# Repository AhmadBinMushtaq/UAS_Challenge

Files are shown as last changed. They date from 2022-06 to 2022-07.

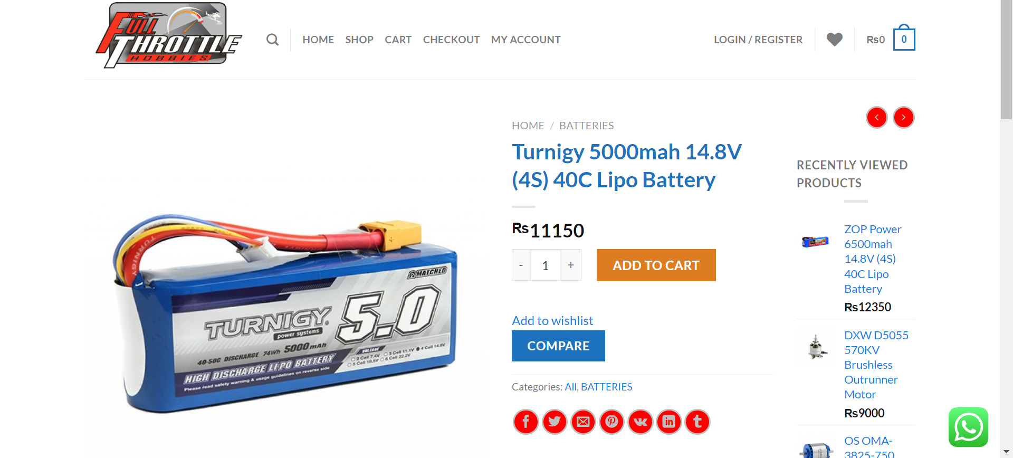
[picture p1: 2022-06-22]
Power & Propulsion System/Turnigy 5000mah 4S.png

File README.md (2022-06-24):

# ***UAS_Challenge***
## **The Hive**

The Hive is a team participating in UAS Challenge 2022 from NUST & FAST. Team consists of four mechanical engineering students, three electrical engineering students, a computer science student, a student from Geo-Informatics and a Business student.

## **Critical Design Report**

This repository keeps track of work distribution from Premilinary Design to Critical Design for all 4 teams:

- *Aerodynamic & CAD Design Team*
    - Sarah Naeem
    - Hamza Hussain
    - Jawad Akbar
    - Muhammad Hassan Kazmi

- *Power & Propulsion System Team*
    - Muhammad Hassaan Ghazali
    - Muhammad Ali Khalid

- *Control & Computing System Team*
    - Muhammad Adeel
    - Ahmad bin Mushtaq

- *Spraying Mechanism*
    - Saad bin Tariq

- *Social Media Outreach*
    - Muaz

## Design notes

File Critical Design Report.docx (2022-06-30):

Unmanned Aerial System (UAS) Challenge Pakistan 2022

National University of Sciences and Technology

Critical Design Report – The Hive

Name | University | Major | Standing
Sarah Naeem – Team Lead | NUST H-12 | Mechanical Eng. | Sophomore
Jawad Akbar | NUST H-12 | Mechanical Eng. | Sophomore
Hamza Hussain | NUST H-12 | Mechanical Eng. | Sophomore
Syed Muhmmad Hassan Kazmi | NUST H-12 | Mechanical Eng. | Sophomore
Ahmed Bin Mushtaq | NUST H-12 | Electrical Eng. | Sophomore
Muhammad Hassaan Ghazali | NUST H-12 | Electrical Eng. | Sophomore
Ali Khalid | NUST H-12 | Electrical Eng. | Sophomore
Muhammad Saad Bin Tariq | NUST H-12 | Geo Informatics Eng. | Sophomore
Muhmmad Adeel | FAST NUCES -Isl | Computer Sci. | Sophomore
Syed Muaz Ashrafi | NUST -H12 | BS. Economics | Junior

Team Members

Signature of Compiler – Sarah Naeem

Team Lead – The Hive

Approved by Dr. Kashif Javed

Assistant Professor at SMME NUST

Faculty Supervisor – The Hive

# List of Figures

# List of Tables

# 1. Summary of CDR Report

## 1.1. Proposed Design

This novel design includes a quad tiltrotor fixed-wing UAV configuration with each rotor attached at the ends of the four wings. With a wingspan of 1.44m and a fuselage length of 1.55m, the UAV has a mass of 4 kg, with a capacity of 3kg for pesticide carriage. The maximum spraying capacity of the drone is 3.5L/min.

With a full payload, it can cruise at 15ms⁻¹ consuming only 84 Watts for propulsion. The drone can fly at 30ms⁻¹ (max. airspeed for the required mission) with rotors burning only 452 Watts. The UAV can achieve a 55ms⁻¹ airspeed (not employed in the current mission) with its 12.5kg maximum thrust.

The spraying mechanism includes two types of nozzles for spraying and misting to maximize spray quality and reduce pesticide consumption per acre. The pump has a BLDC motor for controllable flow and a maximum pressure of 1MPa at 40 Watts power consumption.

Selig S1210 & S1223 are used as front & rear wings airfoils giving the optimum lift-to-weight ratio of wings.

This report provides a thorough analysis and calculation of the drone's mission performance, manufacturability, procurement, and mitigation of all possible safety hazards. This UAV is capable of:

- Stable flight in vertical mode due to widely spaced rotors from the fuselage
- Powerful horizontal flight via thrust from all four rotors positioned horizontally
- Stable transition in flight modes due to variable tilting angles of rotors

Compared to typical fixed-wing and multi-rotor configurations, this configuration produces optimum results as an agriculture UAV for the required mission profile. Comparison with other configurations results in:

- 5.5 to 6 times more power efficient in horizontal cruise than multi-copters. i.e., suitable for spray zones far away from Ground Control Station (suitable for the longest route of 4km in mission)
- Higher precision in spraying than fixed-wing configuration due to capability of hovering, gliding, and staying at transition state while spraying
- More stable hovering and spraying than its parent configuration quad plane

Team Name | | The Hive
Review Items | | Refer below to section 1.2.

Changes since PDR
Change | Reason
The High wing configuration is replaced with a mid-wing configuration.
Aft conventional tail type is replaced with cruciform aft tail configuration.
TMotors MN5008 are replaced with EMAX GT-2826 KV860 | Tmotors are not available locally, and the team changed it to EMAX due to temporary import restrictions
6S Battery is replaced with 4S | EMAX GT-2826 KV860 requires a 4S Battery
Supervisor | | Dr. Kashif Javed – Assistant Professor at SMME
Team Lead | | Sarah Naeem

Table 1. Summary chart for CDR

## 1.2. Payload & Mission summary

The UAV will carry the load at its maximum capacity, i.e., 3kg. It will follow the longest route of 4km towards the spraying zone at a cruise speed of 15ms⁻¹, ideally consuming 266 seconds and 7.75Wh energy. The UAV will cover the complete spray zone in 118-125 seconds, following its optimal path for the least time consumption, consuming 32Wh energy. UAV will then cruise back to landing at 10.7ms⁻¹, consuming 47 seconds and 0.65Wh energy. Hence, including 3 seconds of takeoff & 5 seconds of landing, and a transition time of 1.7 seconds, UAV will complete the mission in 441-455 seconds using the optimum energy consumption approach. It is adopted in this mission since time is not an issue and completing the mission before 10 minutes does not end up in bonus points. However, in real-world scenarios in an emergency, this UAV can complete the same mission in <290 seconds with only 28% more power consumption. Details are provided in the Engineering Analysis part.

2. Project Management

## 2.1. Progress Review

Sr # | Designation/subgroup | Name(s) | Assigned tasks and roles
3. | Mechanical design | - Hamza Hussain - Jawad Akbar - Sarah Naeem - Syed Muhammad Hassan Kazmi | - Aerodynamic Analysis - Structural and stress analysis - CAD model - Airframe manufacturing and material selection
4. | Electrical Circuitry | - Ali Khalid - Muhammad Hassaan Ghazali | - Propulsion system design - Electrical component selection - Battery performance analysis
5. | Spraying Mechanism | - Muhammad Saad bin Tariq | - Spraying mechanism selection - Selecting suitable pump, nozzles and supporting components - Spray tank design and manufacturing
6. | Business Model | - Syed Muaz Ashrafi | - Outreach - Industry support and collaboration - Business model
7. | Control & Computing System | - Ahmed bin Mushtaq - Muhammad Adeel | - Control and computing system design - Selecting supporting hardware

As the preliminary design review mentioned, the team is subdivided into groups for more accessible communication and effective workload distribution. The previous division has been revised since and is given in table 1.2

Table 2.1.1. Team Division and description

The workflow in Figure 2.1.2. shows task division from the PDR up to manufacturing and is divided according to the groups mentioned in Table 2.1.1.

A team tracker on the Google Drive Shared folder tracks the progress & timeline of each team till the CDR. Figure. b.b.b shows a part of The Hive Tracker.

All files in the project, including CAD models, reports, simulations, and source codes, are managed on Google Drive & GitHub repository [1] shown in Figures 2.1.3 & 2.1.4, respectively.

Moreover, the team conducted weekly joint team meetings, occasional team meetings with the faculty advisor and regular meetings of different groups to ensure timely completion of work and maintenance of the Project Progress tracker. Communication is done via MS Teams for meetings, WhatsApp groups for regular updates and Emails for notifications & announcements.

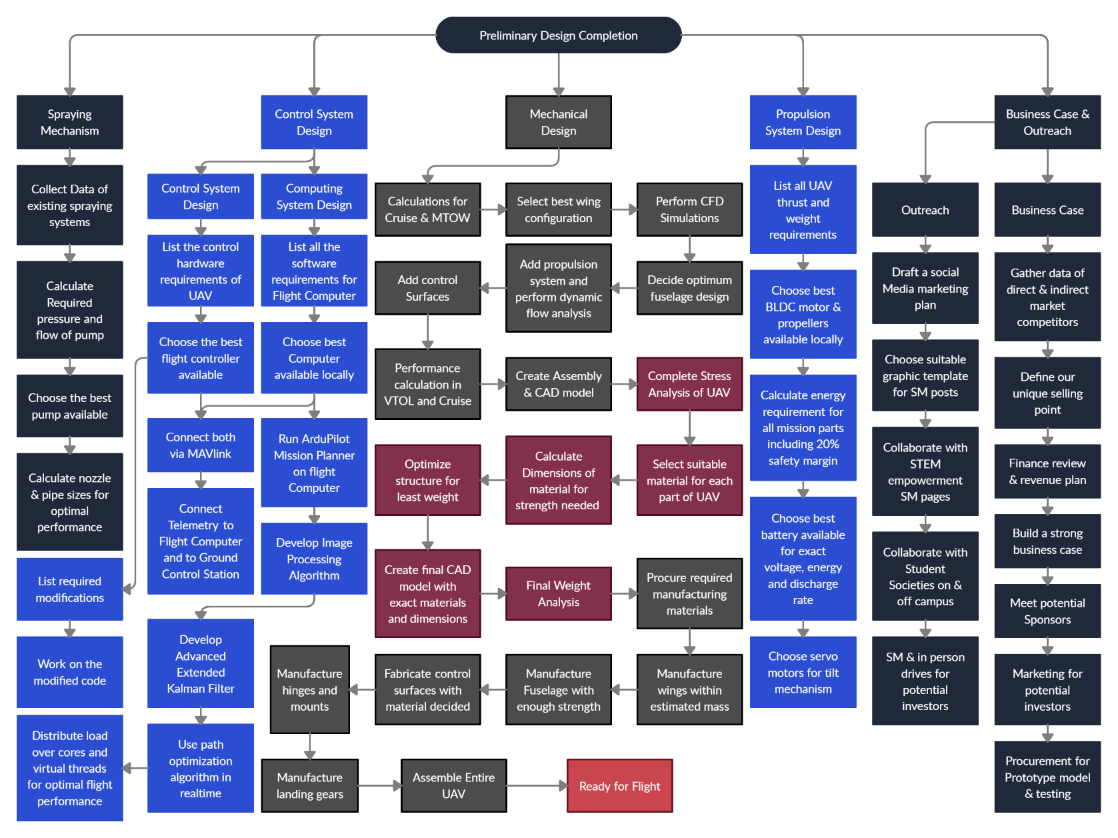
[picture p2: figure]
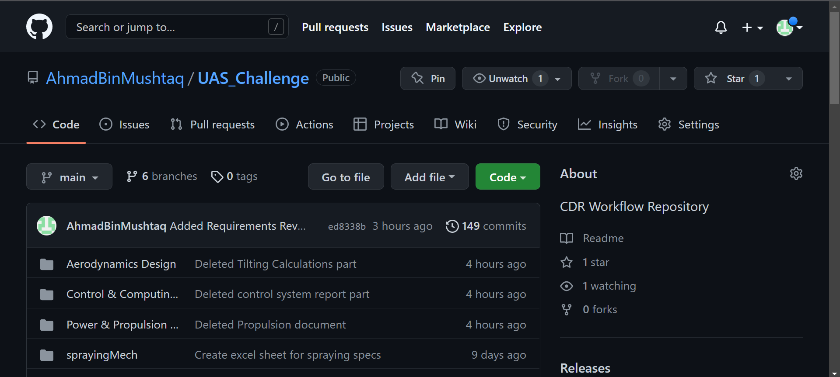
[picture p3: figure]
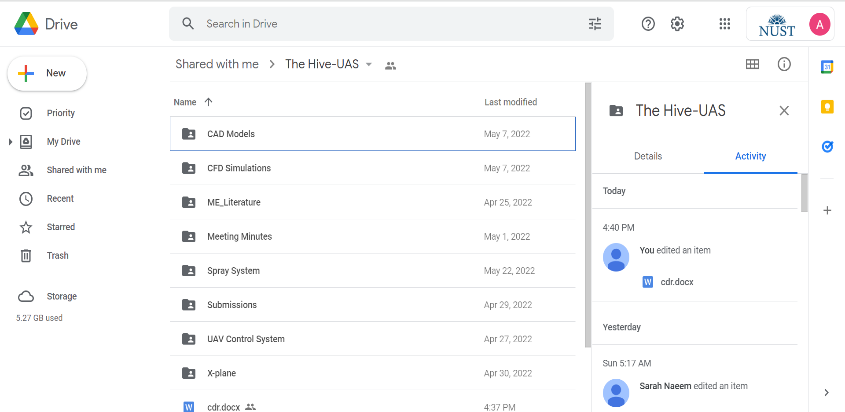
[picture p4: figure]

Figure 2.1.2. Project Workflow after PDR

Figure 2.1.4. Shared Google Drive Folder. [2]

Figure 2.1.3. Shared Google Drive Folder. [2]

## 2.2. Summary of Project Resources, Manufacturing and Risks

Project Part | Human Resource | Other Resources | Procurement | Manufacturing/ Development | Risks | Mitigation
Spraying Mechanism | Saad bin Tariq | None | Nozzles, Pump, Pipes and connectors | Optimized spray tank | Leakage, nozzle blockage, unavailable fluid to inflow. | Sump tank, nozzle filters and good connectors.
Flight Control System | Ahmad bin Mushtaq | ArduPilot source code, Pixhawk 2.4.8 | Open-source software + local available hardware | Fork the ardupilot repo and develop & compile firmware locally | Malfunctioning custom firmware | Continuous trial & error on in real-time flight
Computing System | Muhammad Adeel | Dronekit-python source code, Pytorch, Numpy | Open source | Fork the repo, develop according to needs and use them
Aerodynamic Design | Jawad Akbar | ANSYS Fluent 2022 | NA | Design revaluation in case of unstable flight | Unfavorable lift/drag generated during flight. | Thorough CFD simulation and performance calculations.
Structure Design & Stress Analysis | Hamza Hussain Sarah Naeem | ANSYS Workbench | NA | Design revaluation in case of abnormal stress generation | Airframe damage. | Thorough calculations and appropriate manufacturing techniques
CAD model | Hamza Hussain Muhammad Hassan Kazmi Sarah Naeem | Solidworks 2022 | NA | NA | Improper dimensions used in model leading to errors in manufacturing | Thorough revaluation
Manufacturing | | CAD model, equipment | Raw material | Airframe, tank, supports | Material damage and injuries | Manufacturing under experienced personnel guidance.
Propulsion System Design | Muhammad Hassaan Ghazali | None | All hardware components | None | Faulty parts. Part damage & malfunction mid flight | Procurement from well known vendors. Proper connections.
Battery & Power distribution design | Ali Khalid | None | All components | None | Battery hazards | Employ safe battery practices.
Social Media Outreach & Busin ess Case | Muaz | Social media accounts. Graphic design software | None | None | Digital backlash. | Practice healthy cyber habits.

Table 2. Project resources, manufacturing, and risks

# 3. Requirement Review

## 3.1. Mission Requirements and Verification

For table 4, the term ‘shall’ label a mandatory requirement and the term ‘should’ designates a highly desirable requirement.

Requirements | Verification
A detailed CAD assembly with emphasis on feasibility of design and manufacturing, control capacity and airworthiness. | Detailed CAD assembly created on Solidworks 2022 includes all components and structures employed in the final design.
UAS shall have either a fixed wing, rotary wing, or VTOL airframe configuration. | The design is tilt-rotor transition, fixed-wing VTOL aircraft
MTOM including payload and UAS shall not exceed 6.9 kg. | In weight analysis, the total mass with full payload is 6.9kg
UAS design should cater to rapid assembly/disassembly. | Easy to assemble airframe.
The UAS shall navigate waypoints and spray at targeted area in a fully autonomous manner and it should carry out fully autonomous take-off and landing. | Control & Computing System enable complete autonomy during take-off, spray & landing along with some advanced computing features.
The payload shall be a minimum of 500 ml. | There is 3L payload
The spray tank material should comply with UL 94, V0 flammability standards. It can be detachable or fixed to the UAV. For detachable tanks, re-attachment must be possible within the shortest amount of time. | Fixed spray tank manufactured from Carbon fiber is employed.
UAS airframe shall be designed from scratch. | Entire airframe is self-manufactured.
Cost for COTS components shall not exceed PKR 250,000. Proposed design solutions should be cost-efficient. | Total cost for COTS items adds up to 146K which is well below the specified limit.
Radio Equipment shall comply with PTA directives and licensed for use in Pakistan with a reliable operating range of 1km. Control of the UA and the FTS is ‘spread spectrum’ complaint to 100mW spread spectrum configuration to IR2030 and CE marked 4. | 433 MHz 500MW Telemetry used with range of 2.5km and spectrum available for personal/household devices
UA shall automatically return to landing zone/take-off or activate flight termination after a loss of data link of more than 30 seconds. | Advanced RTL feature in case of disconnected telemetry
UA shall automatically terminate flight in case of loss of GPS signal, for more than 3 minutes. | Flight termination feature included in the flight control system
‘Return Home’ signal shall be capable of activation by safety pilot. | Available in Mission Planner for Ground Control Station
A separate GPS data logger shall be fitted on top of the UAV, with clear exposure to the sky allowing real-time GPS information recording from take-off till landing. It shall also provide post-flight evaluation of the 3D trajectory. Placement of tracker should comply with vehicle safety and provide a glitch free flight safety review. | Provision has been left in design for GPS data logger and the control system is also compatible with it.
UAS design should plan on a target mission flight path with a distance of 2-4 km, from take-off to landing. | (With ref to battery consumption)
UAV to operate further than 500 m up to 1000 m where it may be flown safely and tracked within segregated airspace. | Telemetry used in UAV allows safe communication up to 2.5km range
UAV shall fly at a maximum altitude of 100m. | UAV is designed to cruise at about 30m AGL
UAV shall operate from within 10m x 30 m box, oriented at 30 degrees of wind direction. Landing must be within box, may be touchdown or roll out. | UAV shall use advanced computer vision to detect exact landing position and shall land with centimeters precision
Ground control station shall display all required information and be visible to operators, flight safety officers and judges. | Using telemetry, flight data logs are sent to ground control station using MAVlink and are displayed in mission planner
Should operate in winds of 20 kts gusting up to 25 kts and light rain. Shall be capable of landing and take-off in crosswind components to runway of 5 kts with gusts of 8 kts. | Drone shape designed for minimum air friction caused by wind High Thrust motors used for powerful propulsion against any windspeed below 55kts
Maximum airspeed in level flight shall not exceed 60 KIAS. | 35-40 KIAS adequate for completing the mission. Motor thrust will be adjusted accordingly.
Design and construction shall employ good design practice and use appropriate materials and components. | All materials and manufacturing methods are finalized after a thorough market analysis.
Design shall be supported by satisfactory structural integrity, stability and control, flight and navigation performance and reliability of critical systems. | Balsa airframe with carbon fiber reinforcements for structural integrity. Pixhawk, GPS and image processing for flight control and navigation.
Batteries used shall contain bright colors for easy detection in the event of a crash. | Battery pack will be bright colored.
At least 25% of upper, lower and each side shall be a bright color to facilitate visibility in air and event of a crash. | The entire external surface will employ surfacing of bright colored sheets.
UA shall remain within VLOS of remote pilot and remain below 100m AGL. | UAV path trajectory will make sure that it remains in boundaries
UA shall not be flown within 30 m of any person/structure not under the control of the Remote Pilot. During take-off and landing, it shall not be flown within a 10m distance. | UAV will not cruise below 30m in horizontal flight and would follow the exact trajectory where no humans intervene
UA shall remain in controlled flight and within the demonstration zone boundary during the entire flight | Safety precautions and settings are all set in flight control system
UA appearing uncontrolled or moving into ‘No Fly’ zone shall be subjected to manual override, failure to do so shall activate flight termination. | Safety precautions and settings are all set in flight control system
Consideration should be given to environmental impact. | BLDC motors with minimum noise production are used and environmentally friendly practices are employed for manufacturing.

Table 3. Requirement Review

## 3.2. Mission Success Criteria

The mission will be considered a success if the following criteria are met:

I. The UA covers the longest distance path to reach the SZ and navigate all WPs.
II. The UA completes the entire mission within 10 minutes.
III. The UA carries adequate payload to effectively spray entire spray zone.
IV. The UA performs successful flight termination and manual override.
V. The UA performs controlled flight without any damage to itself, property, or people.
VI. No safety violation occurs.

# 4. Design Description

## 4.1. Design Rationale

### 4.1.1. Airframe

A fixed-wing airframe design has opted for our UAV with a double pair of wings placed along the same axis. The wings are positioned midplane to the fuselage with a tilting rotor on each wing. This orientation provides the desired weight, strength, and performance efficiency in our mission objectives.

#### 4.1.1.1. Wings

Our design includes two rectangular mid-wing pairs, placed one after the other, with a taper ratio of 1 and a dihedral angle of zero. The design follows a primary unswept wing with an aspect ratio of 7.2 (low aspect ratio). A lower aspect ratio allows for easier maneuverability which is one of the core requirements of our mission.[3]

The wingspan of both wings is approximately 1440 mm. The airfoil in the leading pair of wings is S1210[4], oriented at zero degrees. The trailing wings use S1223[5], oriented at five degrees. Each wing section has a chord length of 200 mm. The chosen orientation and dimensions provide us with the ideal amount of lift, cruising speed, and altitudes required for the fly-off mission. A skeletal structure composed of balsa cross-sections and longitudinal spars will provide the main frame of the wings. This frame is reinforced by high-strength and lightweight circular rods running along the entire wingspan. The frame is surfaced to provide a smooth, streamlined surface for good aerodynamic performance.

Each wing will house a 9 g servo and a 20 g servo for the ailerons and tilting rotors. Rubber pipes will also run along its length with the spray nozzle attached at one end and to the pump at the other. Balsa wood cross-sections are placed perpendicular to the longitudinal-lateral plane. These cross-sections will be manufactured to match the airfoil used. Provisions for support rods, servo motors, wiring, and spray system are provided in these cross-sections.

The wings can be detached from the main assembly through simple reinforced connections to allow rapid assembly/disassembly. The details for these connections are discussed extensively in the manufacturing portion.

#### 4.1.1.2. Empennage

The Empennage refers to the tail section composed of a vertical and horizontal stabilizer. The UAV will ideally cruise at a zero-degree pitching angle at all times. The Sum of moments along all three axes must then always be zero. Due to the presence of 4 tilting rotors with relatively large propeller blades, a wake region will be generated. This wake must not blanket our tail sections, significantly reducing control efficiency. Our Empennage must also be lightweight and provide sufficient Control. For this, a cruciform tail orientation has been opted for. It is a type of aft tail configuration, intermediate between the conventional and T-tail, where the vertical and horizontal tails form a '+'. It combines the benefits of both and reduces several drawbacks of both tail configurations. [8] If aligned properly, a deep stall is avoided while maintaining low wing weight. Section 4.2. further shows calculations for the tailplane area. Control Surfaces are discussed ahead.

#### 4.1.1.3. Fuselage

For finalizing the fuselage design, a fuselage design requirements verification rubric was employed. Table 2. summarizes the final optimized design.[6]

Design Requirement | Verification
Adequate space to house payload and system hardware. | The mounting plate runs through the entire length of the fuselage with a payload tank mounted between it. Sufficient free space remains after the assembly of all components.
Low weight. | A monocoque structure is employed using balsa wood bulkheads and reinforced longitudinal spars. It is covered using heat shrink iron-on model aircraft covering (7.7g/ sq. ft.).
It provides a sturdy mounting platform for landing gear. | The landing gear mounts are reinforced at the main mounting plate.
Generates the lowest drag possible. | Low wetted and side area with a streamlined nose and symmetric, streamlined contours result in minimum drag.
It maintains external symmetry. | It has an elliptic shape, symmetric about the longitudinal axis
Airworthiness and compatibility for flight during weather conditions are mentioned in mission requirements. | A sturdy airframe and high-strength iron-on covering are resistant to high winds & gusts and light rain (tensile strength 1,757 kg/sq cm [7]).
Manufacturing feasibility | Semi-monocoque structures have better manufacturability than monocoque designs with increased strength than truss assemblies. Locally available material and manufacturing methods are employed for easy access and guidance on equipment handling.
Structural Integrity and strength | Truss elements are employed where necessary, reinforced by balsa cross-sections along the longitudinal axis and interlinked support structures allowing loads to be distributed over the entire assembly.

Table 4. Fuselage Design requirements and verification

#### 4.1.1.4. Landing Gear

The landing gear is essential for safe takeoff and landing and, if designed well, can act as a shock absorber during crash landings. It must be made of appropriate material to avoid shock caused by harsh and crash landing from traveling through the Airframe. For our design, skids are selected as landing gears. These are fixed supports that are attached to the UAVs. These are widely used in VTOLs as there is no need for wheels. The design employs a four-piece landing gear in table-leg orientation. In this type, four rods are connected to the fuselage via hinges. The rods are fastened to one another via a rubber or elastic strip, resembling a table leg. The material chosen is carbon due to its lightweight and high-strength properties. In the event of a crash landing, the rubber material and the hinges provide a damping mechanism; hence, the material breaking chances are low. The landing gear will widen when the UAV lands, but the rubber provides a restoring force to limit this expansion. This action-reaction force pair causes damping and absorbs the shock that the UAV experiences. In case of a crash landing, only the components damaged are repaired or replaced. Unlike most landing gear systems, the entire assembly will not be replaced.

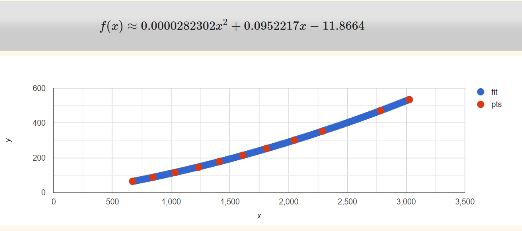
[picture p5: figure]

### 4.1.2. Propulsions

Power & Propulsion system of this UAV consists of following:

- 4 EMAX GT-2826 KV860 Brushless Motors
- 14*7’’ Carbon Fiber propellers
- Turnigy 5000mAh 4S Li-Po Battery with 40C Discharge Rate

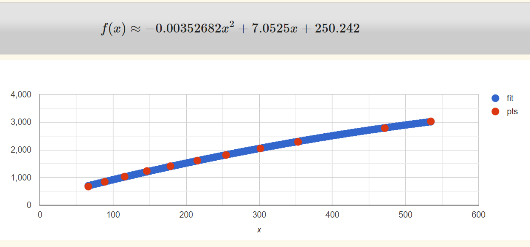
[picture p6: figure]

- 20g servos for tilting individual rotors

Figure 1. Power as a function of Thrust

Figure 2. Thrust as a function of Power

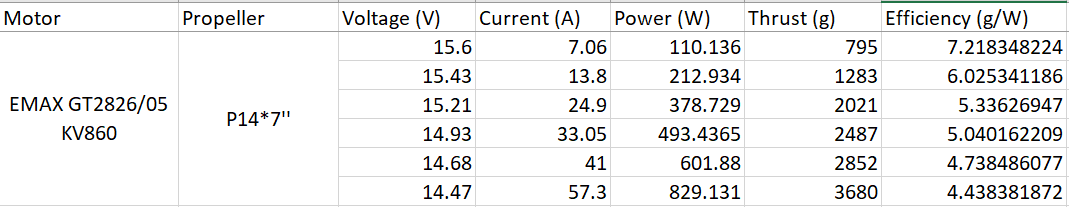
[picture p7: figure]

These components are selected after extensive calculations for optimum performance in fly-off mission. Note: MN5008 mentioned in PDR is replaced by EMAX because it wasn’t locally available.

Figure 3. EMAX GT2826/05 KV860 performance values

Data of all locally available motors is collected into the GitHub repository. The detailed datasheet of EMAX motors is not available online. All the data from the official website and thrust tests in workshops is gathered using finite values for this motor and datasheets available for similar motors; the closest continuous function was plotted against experimental values of thrust & power as shown in Fig. 4 & 5. Below are some power & thrust specifications of the motor used. Thrust for a single motor is written as a function of power using an online function calculator as:

thrust= -0.001632532∙power^2 +5.3238∙power+250 --- (i)

This continuous function gives a precise value for power between 50-850 Watts. Lift & Drag values for the Airframe on different airspeeds were obtained from simulations (detail in aerodynamics section). Again, using finite values, the estimated function was plotted for both lift & drag against airspeed.

lift=0.350317∙v^2 -0.202576 ∙v ---(ii)

drag=0.0350823∙v^2 +0.00372739∙v ---(iii) ∴v=airspeed

Cruise speed is calculated as: lift=0.350317∙v^2 -0.202576 ∙v= total mass of drone

Using this relation, the ideal cruise speed with a full payload, i.e., 6.9kg (flight towards Spray Zone), comes out to be 14.2ms⁻¹, and cruise speed without payload, i.e., 3.9kg (flight back to landing), comes out to be 10.7ms⁻¹.

Power consumption is calculated as:

drag= 0.0350823∙v^2 +0.00372739∙v=thrust of propulsion system

The thrust required for a total payload comes out to be 0.727237 kgf (0.181809 kgf for each motor). Power consumed to require this thrust is calculated by eq. (i) It comes out to be 84.5723W (21.143W per motor). Similarly, the thrust required without payload is 0.421658 kgf, and power consumption is 47.8332W. Calculating energy consumption & time taken for ideal cruise flight of 4km from take-off to spray zone and 500m from spray zone to landing:

time= (4000m)/(14.2ms^(-1))+ (500m)/(10.7ms^(-1))=328.42s (Approx. 5_2^1 minutes)

energy=84.5723W∙281.7s+47.8332W∙46.7s≈7.2383 Wh (<10% of available battery)

Ideal time & energy consumption calculations for takeoff, transition, spray zone & landing were done. Calculations are too complicated to be added in CDR. Results are given below.

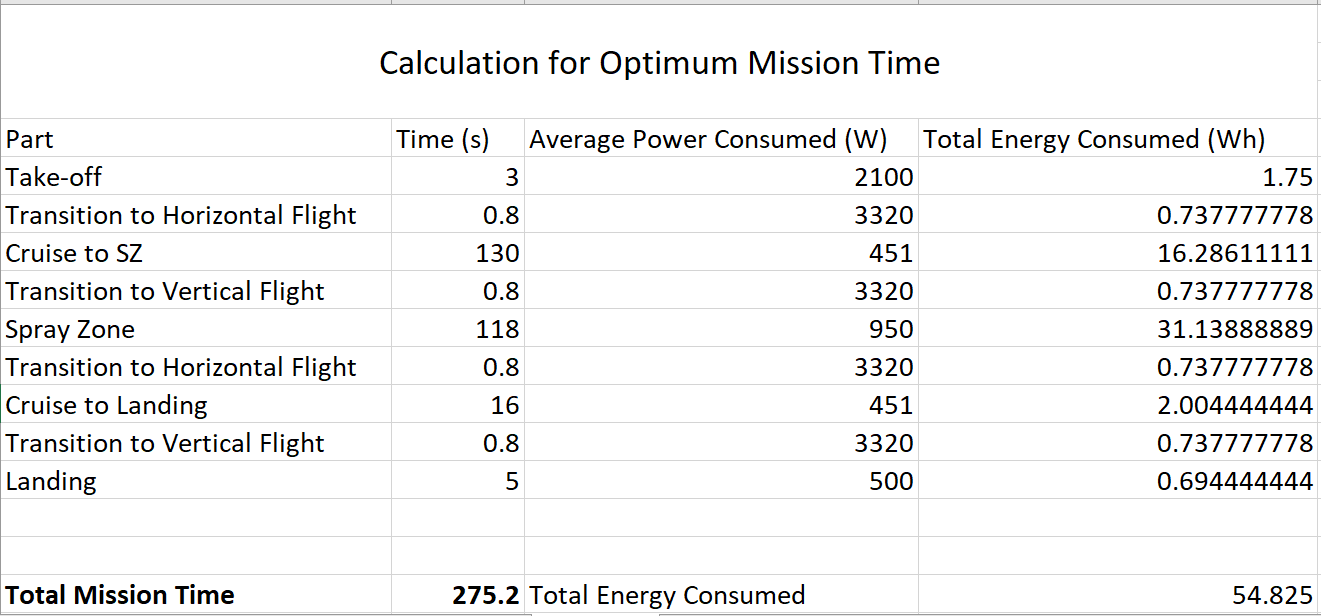
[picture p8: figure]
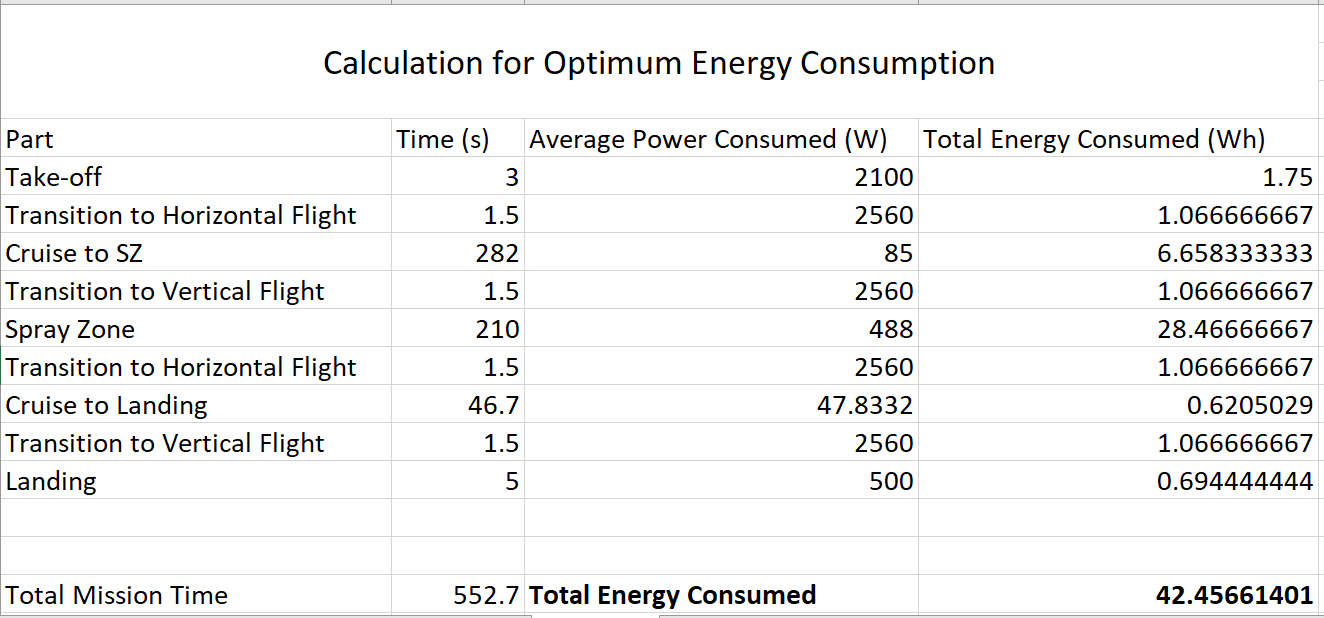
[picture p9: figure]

The battery's energy capacity is 74Wh, about 160% of the total power used in-flight via a 4km route

Figure 5. The calculation for Optimum Mission Time

Figure 4. The calculation for Optimum Energy Consumption

### 4.1.3. Control Surfaces

Controllability is a crucial characteristic of aircraft design. Control is defined as switching from one trim point to another, where trim refers to the state where the summation of forces along all three axes in an aircraft is zero. Control surfaces are employed to achieve controllability. Our UAV design employs the three primary control surfaces; ailerons, rudder and elevator.

#### 4.1.3.1. Aileron sizing

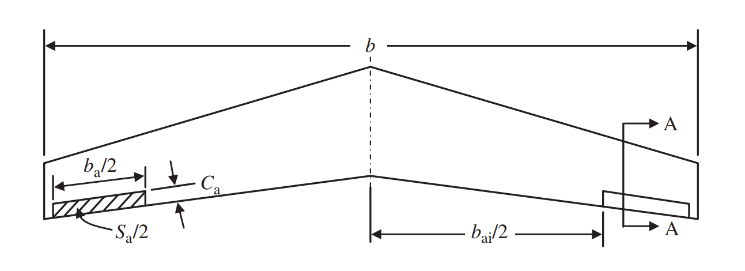
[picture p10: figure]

Two parameters of the aileron, namely the chord length (CA) and total length along the wing (ba/2) will be considered here. A statistical approach has been employed to find the dimensions of the aileron.

Figure 6.vertical stabilizer with labeled aileron variables.[9]

Although many factors influence the chord length of the aileron, one notable consideration is the distance of the rear spar from the trailing edge. The rear spar can serve as a hinge for the aileron, simplifying the design.

In the selected wing airframe, the rear spar is located 0.11 m away from the trailing edge of the wing. The total chord length of the wing is 0.2 m.

C=0.2 m

As per the placement of the rear spar:

C_A =0.11 m [10]

C_A /C=0.55

Now by:

(b_A)/b=(C_A)/C ∴ b=0.61×2=1.22

For either side: b_A /2=0.3355 m [10]

To avoid flow separation, maximum aileron deflection δ_A (positive and negative) will be set at 20 degrees.

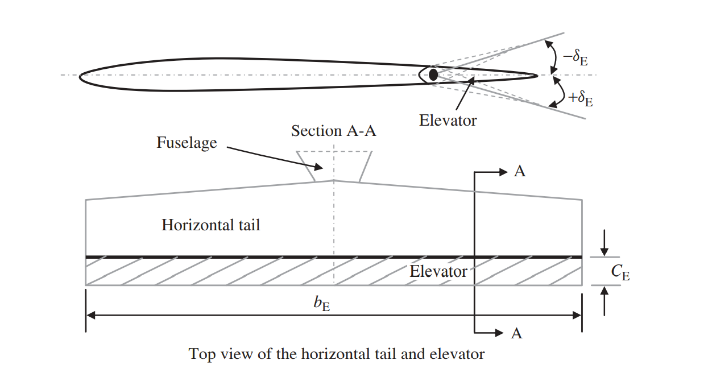
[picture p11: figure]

Elevator design:

The values for surface area and chord length ratios have been selected from the following table for the Cessna 182 due to its smaller size and similar tail geometry to the one selected for the UAV.

Figure 7. Extract from elevator characteristics for common aircrafts. [⁹]

Figure 8. Horizontal tail and elevator [9]

The length of the elevator has been taken equal to the chord length of the horizontal stabilizer, that is:

b_E =0.18 m Chord length of stablizer C_h =0.18 m => C_E =0.44×0.18

C_E =0.079 m ∴C_E /C_h =0.44

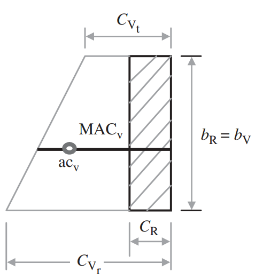
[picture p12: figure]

#### 4.1.3.2. Rudder sizing

Rudder sizing follows a similar approach. A rectangular rudder has been selected for the design. In the design,

b_v =0.188 m b_R =0.188 m [10]

Figure 9. Vertical Tail and Rudder [9]

Figure 10. Extract from Characteristics of Rudder for several aircrafts [9]

Now,

(C_R)/(C_V)=0.42, C_V =0.18 m => C_R =0.18×0.42=0.0756 m [10]

### 4.1.8. Spraying Mechanism

#### 4.1.8.1. Spray Nozzle

Four nozzles will be used at either end of the wings. Nozzles extrude from the wing for easy cleaning and will be connected using 5mm rubber pipes. In addition, connectors will be used for easy and secure connection of the pipes since the wings are detachable; hence, 4 connectors in each wing will ensure no leakage. The pump and the tank will be placed in the fuselage for efficient weight distribution. The nozzle chosen can operate in spray mode and mist mode, providing efficient coverage for the spray zone.

Nozzle Material | Copper | Spray Distance | 1 meter (can be varied)
Spray Flow | 0.2-0.7 ltr/min | Pipe Diameter | 5 mm

Table 5. Spray Nozzle specifications.

#### 4.1.8.2. Micro Diaphragm Pump

A brushless pump is chosen for this mission. The performance details for this model are listed in Table 5. Lightweight and high quality were the main selection criteria for the pump.

Caution: Pump should be used in dry condition, cannot submerge into water.

Voltage | 12 V | Current | 3 A
Flow | 5ltrs/min | Power | 60 W
Pressure | 100 Psi | Connector Size | Fits 6-10 mm inner diameter pipe.

Table 6. Pump specifications

## 4.2. Aerodynamic Analysis

### 4.2.1. Airfoil Analysis

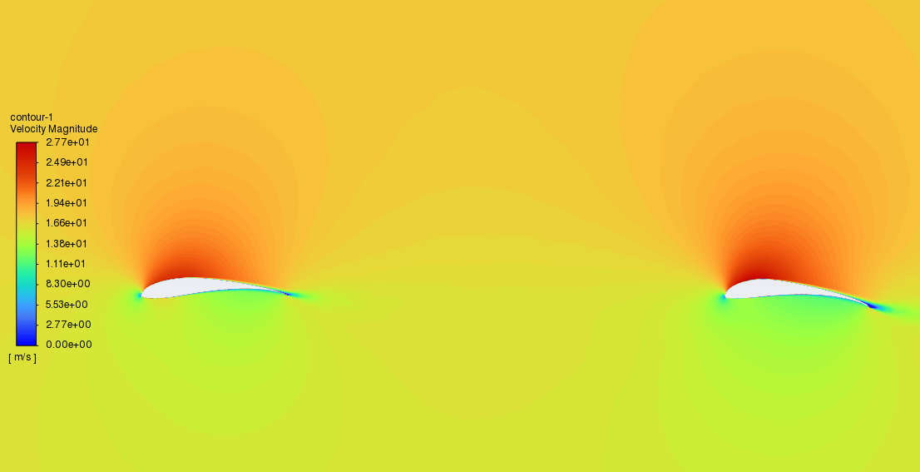
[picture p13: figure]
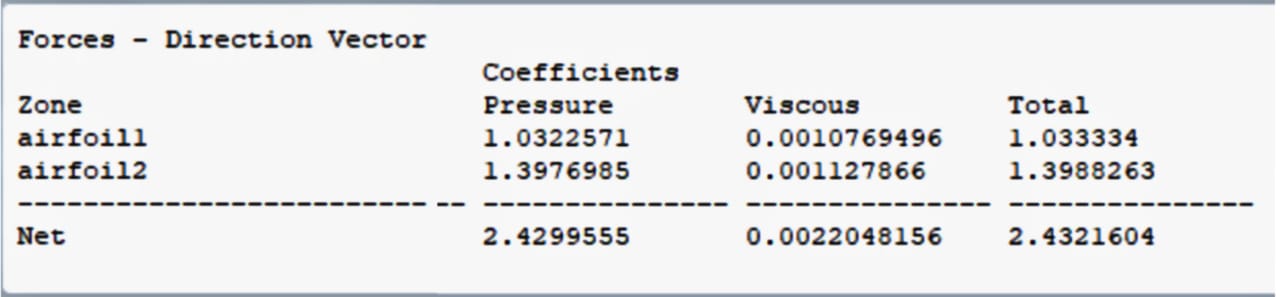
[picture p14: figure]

I Initially, airfoils generating high lift and low Reynolds numbers were short-listed to cope with the mission and efficiency constraints. After an iterative process of combining two airfoils, the best possible combination was selected. The lift curve was obtained using Xfoil. With an upstream airfoil S1210 at 0 pitch, a downstream airfoil S1223 at 5 pitch, a chord length of 200mm for both airfoils and 0.49m between the wings gave a net lift coefficient of 2.43 for Reynold's number of 1.5-2 ×10⁵.

Figure 11. Velocity contour from CFD Analysis for chosen airfoil configuration.

Figure 12. CFD lift force values.

4.2.2. Wing And Fuselage Analysis

With a maximum required force of 6.9kg during level flight the wing area was calculated using

A=(2F_l)/(ρV^2 C_l)

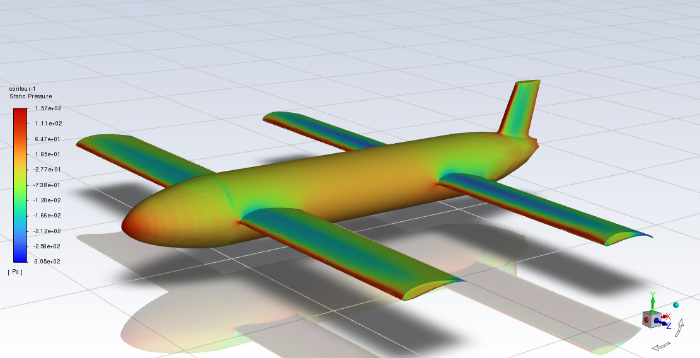
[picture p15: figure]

The shape of the fuselage was kept elliptical to encourage laminar flow over the surface and wing edges, treating it as a streamline body during horizontal cruise. Also, considering it as a blunt body during VTOL and transition state, the elliptical shape reduces pressure drag during vertical flight at much lower velocity than cruise velocity. The nose was kept relatively long to make it sleek and streamline for reduced drag having 254mm length. The fuselage, nose and tail were kept symmetrical about the X and Z axis to avoid any lift generation. The following CAD model was generated for simulation. Simulation was carried out in Ansys® Fluent. The K-Omega turbulence model was opted and a tetrahedral mesh with average mesh size of 50mm and 5mm at fluid and surface zones respectively. [11]

Figure 13. Model Used for 3D CFD simulation.

Figure 14.Pressure contour from CFD simulation of test model.

Figure 15. CFD results for forces along x-axis (drag).

Figure 16. CFD for forces along y-axis (lift).

### 4.2.3. Tail Analysis

The Volume Ratio model is used to compute the tail area. The tail should be sized to generate enough counter torque for adequate stabilization. Reasonable amendments were made to incorporate our design parameters and variation.

C_(HT) =(S_(HT) *L_(HT))/(S_W *c_(MAC)); C_(VT) =(S_(VT) *l_(VT))/(S_W *b)

The values for the volume ratio of horizontal and vertical stabilizers were obtained from the tabulated data in Empennage Statistics and Sizing Methods for Dorsal Fins [8]. The Raymer and Roskam models were used for horizontal and vertical tails, respectively.

The results are concluded that the vertical tail sweeps from 200mm to 160mm chord having a mean chord length of 180mm meters and a height of 188mm. The horizontal tail has a 180mm chord and 820mm span. The horizontal tail is situated midway onto the vertical stabilizer to heighten it and prevent turbulent air from the propeller from disturbing its laminar flow. The aerodynamic center is situated 23.5" from the nose tip.

## 4.3. Structural Analysis

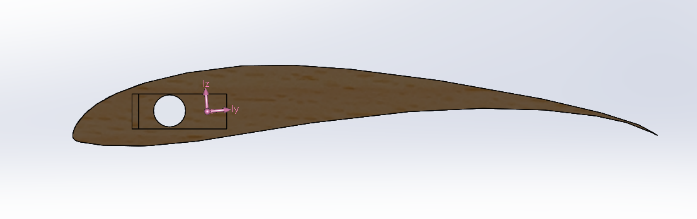
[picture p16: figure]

Bending Moment of wings:

Figure 17. Airfoil Section from wing CAD model.

Centre of mass along x=46.2 mm

Total weight of UAV=6.9kg×9.8m/(s^2)=67.7N

Previously calculated lift force=74 N

rear wing weight=W_(wing,rear) =160.45g=0.16045kg

front wing weight=W_(wing,front) =153.96g=0.15396kg

Assuming that each wing produces 1/4th of the total lift (L). Then the balance of vertical forces for the wings imply:

Front: (For lift=weight of UAV)

V=L/4-W_(wing,front)

V=(67.7/4)-(0.15396×9.8)

V=25.54 N

Corresponding bending moment for center of mass at 0.0462 m:

W=0.0462×25.54

W=1.18 Nm

(For calculated lift)

V=L/4-W_(wing,front)

V=17 N

Corresponding bending moment for center of mass at 0.0462 m:

W=0.0462×17=0.785 Nm

Rear: (For lift=weight of UAV)

V=L/4-W_(wing,rear)

V=15.35 N

Corresponding bending moment for center of mass at 0.0462 m:

W=0.0462×15.35=0.71 Nm

(For calculated lift)

V=L/4-W_(wing,rear)

V=16.93 N

Corresponding bending moment for center of mass at 0.0462 m:

W=0.0462×16.93=0.78 Nm

## 4.4. Performance & Dynamic Analysis

### 4.4.1. Vertical Flight

#### 4.4.1.1. Assumptions

- The UAV experiences negligible friction (drag) in the vertical direction

#### 4.4.1.2. Mathematical Model

For vertical flight, the model is the simplest since drag is neglected. The real-life values will be significantly different, but since only takeoff and landing is vertical, there would be a negligible effect on overall mission time and energy consumption.

Summing all force vectors on UAV, ma=vertical thrust-weight =>a=(thrust-weight)/(mass of UAV)

Acceleration can be written as a power function using the estimated function (thrust as a function of power). Distance traveled can be expressed as a function of total energy consumed, integrating it twice w.r.t time. Optimizing the total energy, we find out that 10.5kgf total thrust for the UAV gives optimum energy consumption for 30m takeoff

Table 6. Vertical Flight Energy consumption

### 4.4.2. Horizontal Flight

For horizontal flight, calculations are simple too. Since the UAV is cruising at constant airspeed and altitude, all vertical components are of no concern; for horizontal components, drag=thrust .

Since lift can be expressed as a function of velocity using Fluent Simulations, velocity from lift=weight comes out to be 14.2ms⁻¹. From this cruise speed, drag can be calculated; hence, the required thrust is calculated using that drag. Since power can be written as a close function of thrust for EMAX GT-2826/5, power consumed can be calculated for the horizontal cruise. Using this methodology, power consumed during the cruise becomes 84 Watts.

Table 7. Horizontal Flight performance.

### 4.4.3. Rotors Transition State

#### 4.4.3.1. Conventions

- Tilt angle in horizontal flight is set as 0o and in vertical flight as 90o.

#### 4.4.3.2. Mathematical Model

For simplicity, we assume that thrust magnitude during the transition phase remains constant and only the tilt angle changes. The thrust provided by rotors is divided into vertical and horizontal components depending on the instantaneous tilt angle.

Table 8. Vector Diagram for Transition state forces.

Vetical Thrust=Weight-lift=Thrust ∙sinθ =>θ=sin^(-1) ((Weight-lift)/(Thrust))---(i)

Horizontal Thrust-drag=ma =>a=(Thrust∙cosθ-drag)/(mass of UAV) ---(ii)

Acceleration of UAV is represented as function of tilt angle & drag force. Tilt angle is a function of lift in (i). Fluent simulations show that drag & lift can be written as function of horizontal velocity as:

drag=0.350317v^2 -0.202576v ---(iii) lift=0.0350823v^2 +0.00372739v---(iv)

Hence, using (i) and (iv), θ can be written as function of velocity.

θ=sin^(-1) ((Weight-0.0350823v^2 +0.00372739v)/(Thrust))---(v)

Using (ii), (iii) & (v), acceleration is written as function of velocity. Hence, equation becomes:

a=(Thrust∙cos⁡(sin^(-1) ((Weight-0.0350823v^2 +0.00372739v)/(Thrust)))-drag)/(mass of UAV)---(vi)

Velocity & Speed are given as: v= ∫_(t_0)^t adt---(vii) distance s= ∫_(t_0)^t vdt---(viii)

The flight controller does not continuously control tilting but controls discretely, i.e., changing every clock cycle, which changes the tilt angle every micro-second according to the equations above.

The easiest and most accurate way to calculate the complete spectrum of tilt angle, horizontal & vertical speed, lift, and drag is to distribute the time domain into discrete parts of microseconds (Δt) and then, from t = 0s & v = 0ms⁻¹, start calculating lift, drag and acceleration. Use v_(i+1) =v_i +a_i Δt---(ix) & s_i = v_i Δt+ 1/2a_i Δt^2 to calculate distance and next interval velocity.

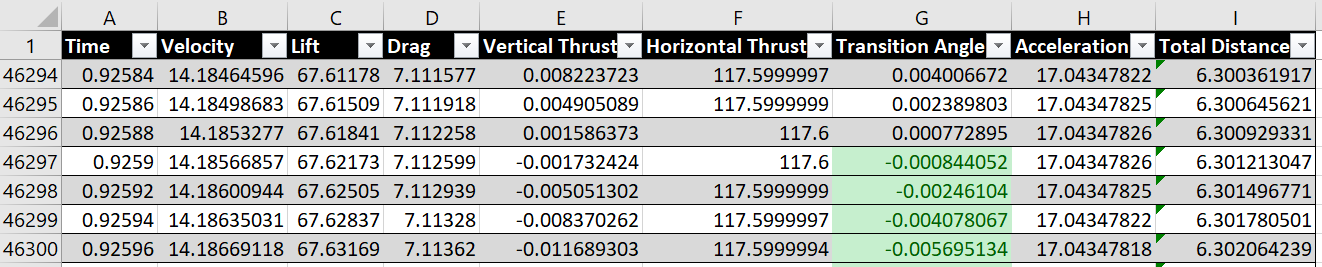
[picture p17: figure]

Calculations for the transition region are made in an excel sheet using this approach, keeping Δt = 20µs.

Table 9. Transition state performance values.

During the transition from 90o to 0o, the time taken is 925ms and the distance covered is 6.3m.

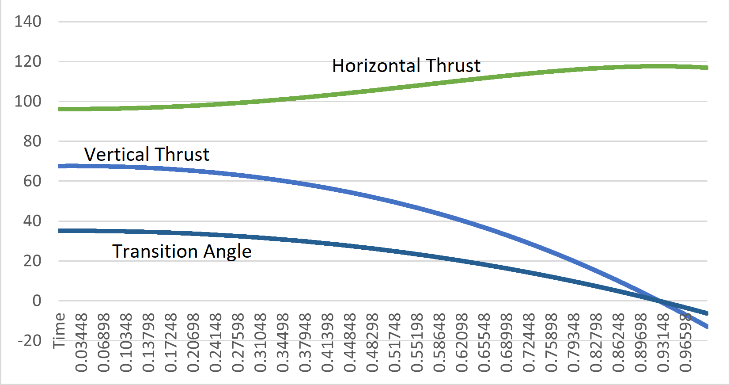
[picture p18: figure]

Note: This calculation assumes that drone acceleration is the bottleneck, not the tilting servo speed because the tilting servo used in this UAV has a higher angular velocity than the transition state.

Figure 18. Drag and velocity variation over time.

Figure 19. Thrust variation over time.

4.5. Weight Analysis

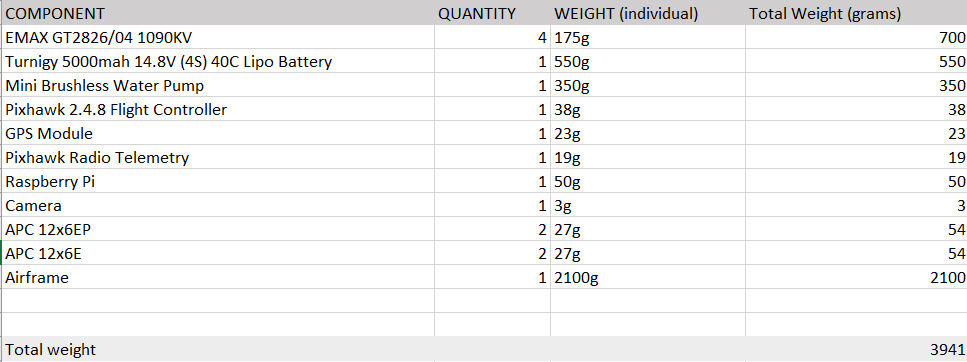
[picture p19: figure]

Weight analysis showed that the combined weight of the UAV and all its components minus the payload is approximately 3.9 kg, leaving behind a 3 kg capacity for payload, which is the ideal amount of fluid required for effective spraying of the entire spray zone. The weight analysis is given in the table below.

Table 10. Weight Breakdown

## 4.6. Control System and Flight Controller

Flight Control System | 1. Pixhawk 2.4.8 (ARM Cortex M4, 6-axis gyroscope + accelerometer, barometer, compass, failsafe co-processor) 2. NEO-M8N GPS Module (Accuracy of 2m & 18 Hz update rate)
Flight Computing System | 1. Raspberry Pi Model 4 B (4GB RAM) 2. Raspberry Pi Night Vision Camera (5MP, 1080p)
Telemetry | 1. 433 MHz 500mW radio telemetry (2.5km range

The Control & Computing System hardware consists of:

Table 11. Control System Components

The hardware for the control system is selected after a detailed analysis of all available options in terms of cost (time & money), reliability, and mission limitations. Control and Computing systems, both are put inside the UAV for two reasons:

- Complete autonomy of UAV: UAV is independent of any ground control station and can complete spraying missions outside the telemetry range with great precision.
- Advanced Computing & Artificial Intelligence: Using HD image processing, machine learning, advanced model-prediction algorithms & artificial intelligence on a powerful quad-core Raspberry Pi, the onboard computing system makes this UAV the first of its type, which outperforms any manual or autonomous agriculture drone in the market.

The controller and Computer are present on different adjacent boards inside UAV. The schematic below shows the rough idea of electrical connections (not the original electrical schematic, just a rough schematic for better understanding).

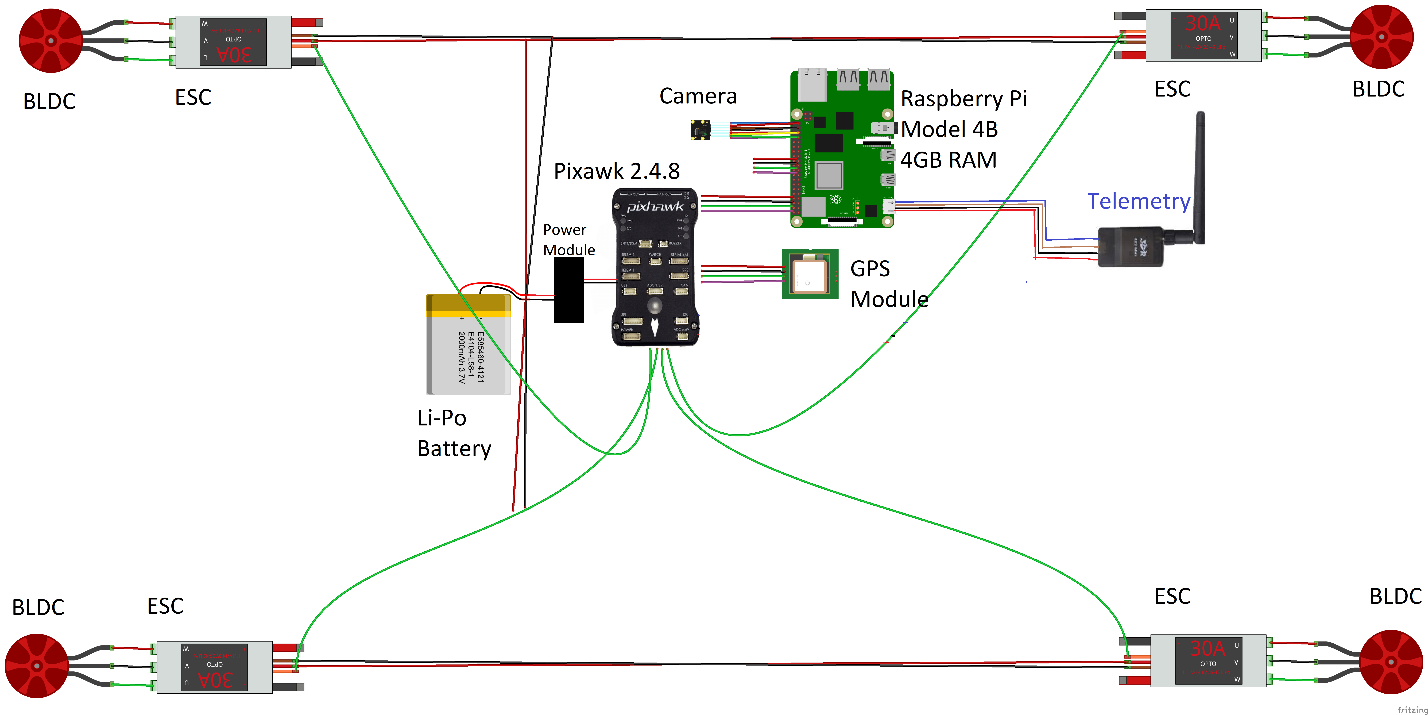
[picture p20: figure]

Figure 22. Control System Schematic

The most optimum approach would be to embed the flight controller (ARM Cortex-M4 + 32-bit failsafe co-processor), all control sensors (MPU6000, ST micro gyroscope + magnetometer), flight computer (ARM Cortex-A72, SRAM, DRAM), and all peripherals on a single PCB. It would significantly reduce the wiring across all avionics. The main issue in this approach is the fabrication of this all-in-one PCB. It is estimated to be minimal of 6-layer PCB with <150µm scale, which is not available in Pakistan. Moreover, designing all connections, power optimization, signal latency & area optimization require more time and effort. Depending on the time & resources available, this does not seem impossible to achieve soon.

### 4.4.1. Flight Controller Software

Pixhawk runs modified ArduPilot firmware for quad tiltrotor UAVs with four rotors tilting. Modifications in the firmware provide optimum performance with our UAV's aerodynamic specifications. Modifications include:

- Vertical to Horizontal or Horizontal to Vertical Flight Transition with variable tilt-angle (enabling both time & energy optimization according to requirements)
- Drone stabilization by controlling four tilting servos on independent PIDs (for optimum stability)
- Shifting Telemetry to Flight Computer to enhance the performance of control loops in-flight Computer since there is only one core in Pixhawk (ARM Cortex-M4)

4.4.2. Image Processing:

The Raspberry Pi Night Vision Camera enables the drone to capture high-quality images during the day and at night. It would allow real-time computer vision in the UAV. We use Open-CV written in C++ for faster image processing.

In addition to Open-CV, the drone uses with YOLO (You only look once) algorithm for real-time object detection using Machine Learning. It would allow the drone to be fully autonomous since it would be able to recognize objects in the images of the camera and make movements according to the landscape.

### 4.4.3. Path Optimization:

The drone should take the shortest path to complete its task optimally. The drone ensures this with the most efficient path optimization algorithms. The drone would use the Traveling salesman problem algorithm to find the shortest Hamiltonian path.

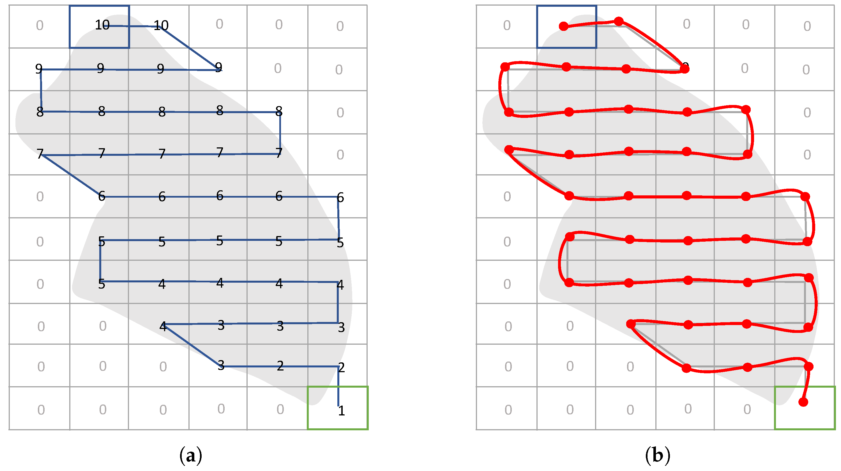
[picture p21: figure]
Drones | Free Full-Text | Survey on Coverage Path Planning with Unmanned Aerial Vehicles

Now the drone has the shortest path(a), but the drone (in fixed-wing mode) cannot completely follow the path generated by the previous algorithm. It occurs due to the speed of the drone and the maximum turn angle of the drone. For the final optimized path, the drone would use the Band-Turn mechanism. It would help the drone achieve the image's path (b). Thus, the drone would use this path to consume the minimum energy needed.

Figure 21. Path Optimization

## 4.5. CAD Model

# 5. Safety Case

All the possible security threats & risks either related to drone hardware or its control system are carefully listed along with the worst-case scenarios for each. These risks are addressed during the design, components selection, software selection, and code modification. Moreover, all the possible security protocols shall be ensured in test flights to minimize casualties.

Out of all these threats & risks, major ones are listed in CDR along with their severity and how we minimized them or aimed to during test flights and final fly-off.

Probability | Severity | Risk | Mitigation
Improbable | Marginal | Pixhawk Processor Failure | - Failsafe 32-bit co-processor
Remote | Minor | Control loop glitch | - Frequent test-flights with deep analysis of flight data log
Improbable | Major | Losing connection between flight controller & flight computer | - RTL or safe landing depending on GPS connection, distance from launch and remaining battery
Remote | Marginal | Motor Failure | - Use state-of-the-art BLDC motors
Occasional | Major | Propeller Failure | - Use Carbon Fiber Propellers
Remote | Major | Battery Failure | - Small Failsafe battery for RTL or immediate Landing
Improbable | Major | Pesticides Tank Leakage | - Carbon fiber as manufacture material, waterproof sheet on electrical components
Improbable | Minor | Pesticide not available to pump inflow | - Sump in tank to ensure steady supply to pump
Probable | Minor | Nozzle Blockage | - Filter in pump inlet
Improbable | Minor | Leakage from pipes | - Good quality connectors & Thermal resistant pipes
Remote | Minor | Aircraft Stalling | - Proper airfoil/angle of attack selection. - Reasonable deflection of control surfaces when operated. - Maintaining cruise speed greater than stalling velocity.
Remote | Marginal | Crash Landing | - Manual override system in place in case of emergency landing. - Proper landing gear installed to bear impact. - Proper material selection.
Occasional | Minor | Unstable flight due to uneven weight distribution | - Proper component sizing. - Properly assembled airframe. - Drag reduction via optimization of aircraft geometry.
Occasional | Minor | Damage to Surfacing Material | - Selection of appropriate material meeting tensile strength requirement. - Provision of clearance from ground in case of impact via landing gear. - Selection of easily replaceable materials in case of minor damage.
Remote | Minor | Damage to airframe in case of impact/collapse of airframe due to load on mount plate | - Selection of appropriate material for airframe possessing suitable mechanical properties. - Structural reinforcement of airframe. - Proper mounting of components on plate and uniform load distribution across mounting plate.
Occasional | Major | Propeller damage during transition phase | - Adequately secure fixture of propeller on shaft. - Selection of appropriate time for transition to avoid unnecessary drag/abrupt flow separation across the propeller blade.
Occasional | Marginal | Li-Po Battery may catch fire | - Charge on cement surface, Store in nonflammable container, do not charge unattended to avoid overcharging.
Occasional | Minor | Li-Po Battery may swell | - Immediately stop charging, store in fireproof container, wait for it go back to normal size, may have to replace battery.
Remote | Major | Battery Short Circuit | - Vigilant wiring and connections of battery for fly-off and charging.

Table 12. Possible risks and their mitigation.

## 5.1. Safety Steps in Control & Computing System Design:

Since the drone is most vulnerable to any bugs or glitches in software, safer software is a higher priority than performance-optimized software for our Control & Computing System team. In this regard, the modifications in the control loop will be used in test flights after being checked by the faculty advisor and will be used in fly-off after multiple test flights without any glitch or unwanted output.

## 5.2. Safety Steps in Propulsion Design:

A safer propulsion system implies a safer flight. Motors & Propellers used in the drone are the highest quality ones available in the market to ensure the safest propulsion system possible. However, to ensure the safety of the electrical motors, it is crucial to take the following precautions:

- Constant troubleshooting to establish whether the features in the motors are working properly
- Do not leave a short-circuited battery for long because it would eventually explode.
- Do not power the motors beyond their voltage capacity.
- Never leave a motor to operate unattended.

## 5.3. Safety Steps in Spray System Design:

Pipes of good quality are used to ensure that there is no leakage of flowing pesticides. The high-quality pump is used to minimize failure probability. The spray tank is designed to minimize leakages in case of a crash.

# 6. Manufacturing & Support

## 6.1. Airframe

The wing airframe will be constructed using ___ balsa wood sections of 5mm width and 10mm width on the ends, which will provide adequate reinforcement and a platform for accurate surfacing. These sections will be laser cut, and holes are measuring 8mm,6mm and 10mm (dia) will be provisioned in them. Carbon fiber support rods of 8mm and 6mm dia will be inserted along the wingspan for effective stress distribution. These will protrude out of the fuselage-end of the wing to provide a platform for insertion into the fuselage, making the wings re-attachable. The spray system pipe will be inserted through the 10mm hole. For further reinforcement and ease of surfacing, the wing's leading edge will be covered entirely with balsa wood sections glued to each other. Similarly, the trailing edge will be solid balsa wood.

Sheeting will be employed to surface the wings. Vinyl wraps will be the material of choice. Provisions for spray system nozzles and aileron servos will be ensured prior to the sheeting to prevent damage to the surface and unnecessary material use.

## 6.2. Spray Tank

The tank to store liquid will be manufactured using a negative mold made of latex rubber. The negative mold is enclosed by a plaster mother mold or retaining mold made with fiberglass to ensure that the rubber will maintain its shape during casting. The carbon fiber with a thickness of 0.46mm will be used as the material to make the tank using the wet lay-up technique. However, the overall tank thickness will be around 0.6 mm as the resin will be applied on both sides.

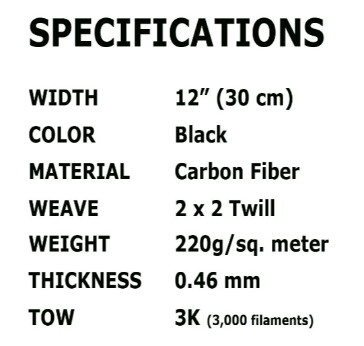
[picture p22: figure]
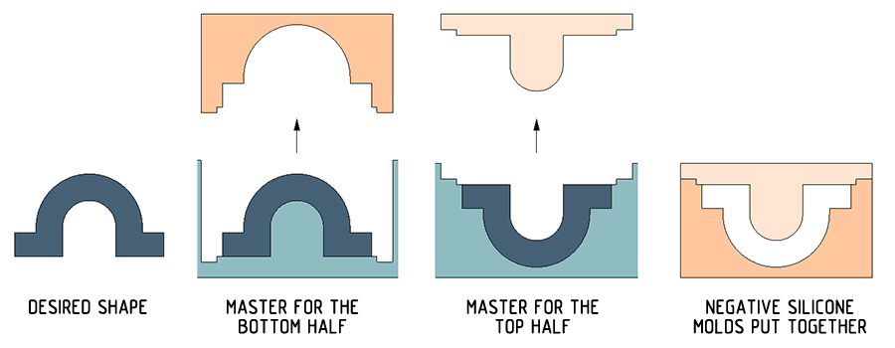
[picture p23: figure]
Week 10 - Moulding & Casting

Wet lay-up involves cutting and laying the fiber into the mold before applying the resin with a brush, roller, or sprayer. This workflow is the least expensive and has the fewest needs to manufacture carbon fiber parts, but it also demands the most expertise to produce high-quality parts.

Figure 22. Selected Carbon Fiber specifications.

Figure 23. Manufacturing process for spray tank. [¹²]

Desired shape in our case is the water/pesticide tank. That tank will initially be made from high density polyethene as it easy to shape it according to the design specifications. For making the master mold the polyethene tank will be covered by thin layer of cling plastic wrap with thickness of 0.02 mm. This is done to prevent any chemical reaction between polyethene and the latex rubber. In addition to that, a releasing agent is used to separate the mold from the object.[13]

In general, carbon fibers have low densities, high thermal and chemical stabilities in the absence of oxidizing agents, and great creep resistance. Furthermore, the strength provided by carbon fiber is very high. Hence, in a situation of a crash the tank will not rupture, protecting the electrical components from the liquid.

## 6.3. Final Assembly

## 6.6. Storage and Handling

## 6.7. Innovation

# 7. Qualification Test Plan

Table 13 provides an overview of the qualification test plan for the proposed UAV design.

Sr no. | Objective | Method | Success criteria | Test Results
| MTOW of 6.9 kg. | Weighted analysis. Weighing scales-fully loaded aircraft with weighted dummy tracker. | MTOW < 6.9kg
| Navigation of way points | Test runs with GPS data logger and inspection of flight trajectory | All waypoints in range of 10 meters of trajectory
| Assembly/Disassembly | Wings capable of detaching | Takes <=5 minutes
| Environment-Friendly propulsion system | Electrical Propulsion System | Doesn’t burn any hydrocarbons
| Minimum payload of 500 ml.
| Fully Autonomous Flight | | Performs take-off, landing, navigation of WP and spraying mission with full autonomy.
| Flight Termination System
| Cost for COTS components | Detailed cost list accommodating shipment cost and 10% provision for price hike. Opting for locally available products. | Less than PKR 250,000
| Airworthiness, control capacity and manufacturability of CAD model
| Tracking System | | Provides both real-time and post-flight evaluation in 3D trajectory
| Landing | | UAS stops within the specified 10 m x 30 m box.
| Ground Control Station
| Airspeed of UA in level flight | | Does not exceed 60 KIAS.
14. s | Radio Equipment | Cross checking for compliance PTA directives and procuring from PTA verified and well-known vendors. | Complaint with PTA directives, licensed for use in Pakistan – operating range 1km, spread spectrum complaint to 100mW spread spectrum confirming to IR2030 and CE 4.
| Weather limitations | | Operates in 20kts winds, gusting to 25 kts and light rain. Successful take-off and landing in crosswind component of 5 kts (to runway) with 8 kts gusts.
| Fuel/battery combination
| Airworthiness | | Controlled flight – remains within demonstration zone boundary. Allows successful flight termination and manual override. Remains in VLOS of remote pilot. Below 100m AGL. Does not fly within 30 m distance of any obj. for takeoff/landing, does not fly at 10 m distance.
| Low environmental Impact. | | Low pollution, fuel efficient, low noise, non-hazardous.

Table 13. Qualification Test Plan.

# 8.0. Cost Analysis

The parts were selected by meticulously cross-checking different vendors according to our weight and thrust requirements; we selected a battery and motor for our UAV. For our flight computer, we used a raspberry pi and Pixhawk microcontroller. We had to select components that were compatible with it, such as a camera, GPS module and a telemetry system.

Our materials are sourced locally from well-known and trusted vendors. Our three leading vendors were:

Full throttle

Arctic Hobbies &

Electrobes

We ensured that the total cost of our COTS materials remained well below the limit given in the competition rules.

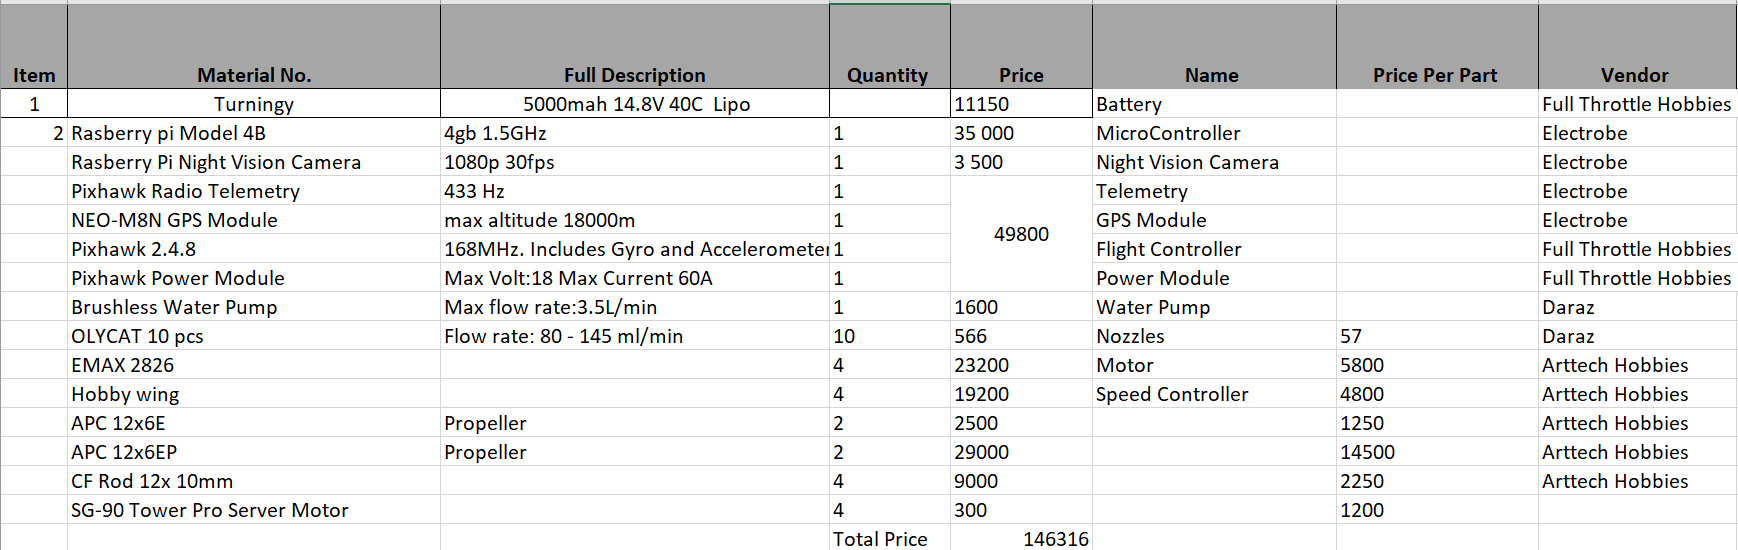
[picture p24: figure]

# References

[1] GitHub Repository. AhmadBinMushtaq. UAS Challenge. Github. https://github.com/AhmadBinMushtaq/UAS_Challenge

[2] The Hive-UAS. Google Drive. https://drive.google.com/drive/u/0/folders/1elPmgAiqRSWPfUWt-iwANOj1h2q9I6HO

[3] Sadraey M H. (2012). Chapter 5: Wing Design. Aircraft Design: A Systems Engineering Approach. Chichester, West Sussex, U.K. Wiley. https://download.e-bookshelf.de/download/0003/8236/25/L-G-0003823625-0002286103.pdf

[4] S1210 12% - Selig S1210 high lift low Reynolds number airfoil. Airfoil Tools. http://airfoiltools.com/airfoil/details?airfoil=s1210-il

[5] S1223 – Selig S1223 high lift low Reynolds number airfoil. Airfoil Tools. http://airfoiltools.com/airfoil/details?airfoil=s1223-il

[6] Sadraey M H. (2012). Chapter 7: Fuselage Design. Aircraft Design: A Systems Engineering Approach. Chichester, West Sussex, U.K. Wiley. https://download.e-bookshelf.de/download/0003/8236/25/L-G-0003823625-0002286103.pdf

[7] Product Specification. MonoKote cub yellow 6’. Horizon Hobby. https://www.horizonhobby.com/product/monokote-cub-yellow-6/TOPQ0220.html

[8] Sadraey M H. (2012). Chapter 6: Tail Design. Aircraft Design: A Systems Engineering Approach. Chichester, West Sussex, U.K. Wiley. https://download.e-bookshelf.de/download/0003/8236/25/L-G-0003823625-0002286103.pdf

[9] Sadraey M H. (2012). Chapter 12: Design of Control Surfaces. Aircraft Design: A Systems Engineering Approach. Chichester, West Sussex, U.K. Wiley. https://download.e-bookshelf.de/download/0003/8236/25/L-G-0003823625-0002286103.pdf

[10] Bayati A., Reinders P. (2021). Part B: Flight Performance and Flight Mechanics. Conceptual Design of a Small Size Unmanned Air Vehicle. https://www.diva-portal.org/smash/get/diva2:1572108/FULLTEXT01.pdf

[11] Anderson J D. (1999). Aircraft Performance & Design. McGraw-Hill Science Engineering. https://www.academia.edu/40606141/AIRCRAFT_PERFORMANCE_AND_DESIGN

[12] Alex J. Week 10 – Molding & Casting. Fab Academy. https://fabacademy.org/2019/labs/kochi/students/joel-alex/week10.html

[13] How to Manufacture Carbon Fiber Parts? Form labs. https://formlabs.com/asia/blog/composite-materials-carbon-fiber-layup/

# Bibliography

M H Sadraey. (2012). Aircraft Design: A Systems Engineering Approach. Chichester, West Sussex, U.K. Wiley. https://download.e-bookshelf.de/download/0003/8236/25/L-G-0003823625-0002286103.pdf

J D Anderson. (1999). Aircraft Performance & Design. McGraw-Hill Science Engineering. https://www.academia.edu/40606141/AIRCRAFT_PERFORMANCE_AND_DESIGN

Raymer D P. (1989). Aircraft Design: A Conceptual Approach. Washington, D.C. American Institute of Aeronautics and Astronautics. https://vdoc.pub/documents/aircraft-design-a-conceptual-approach-4ej7ve6p7700

Varsha N, Somashekar V. (2018). Conceptual design of high-performance Unmanned Aerial Vehicle. IOP Conf. Series: Materials Science and Engineering 376 (2018) 012056. https://drive.google.com/drive/u/0/folders/1hOUyhr7jtv65HLhXofrR8VwvRt0HjL8d

Sharma S, Sharma R, Kumar V, Chandel S. (2021). Analysis of a Tiltrotor Vertical Take-off and Landing Unmanned Aerial Vehicle: CFD Approach. IOP Conf. Series: Materials Science and Engineering 1116 (2021) 012096. https://drive.google.com/drive/u/0/folders/1hOUyhr7jtv65HLhXofrR8VwvRt0HjL8d

Tahir T. (2007). Manufacturing and structural analysis of a lightweight sandwich composite UAV wing. The Graduate School of Natural and Applied Sciences of Middle East Technical University. https://etd.lib.metu.edu.tr/upload/12608774/index.pdf

Ling A E. (2012). Design and Manufacturing of Generic Unmanned Aerial Vehicle Fuselage Assembly (Payload Bay, Empennage, Wheel Assembly and Wingbox) via Low Cost Fiber Glass Molding Process. Faculty of Engineering and Sciences University Tunku Abdul Rahman. http://eprints.utar.edu.my/542/1/MH-2012-08UEB05561-1.pdf

Muraoka K, Okada N, Kubo D. (2009). Quad Tilt Wing VTOL UAV: Aerodynamic Characteristics and Prototype Flight Test. American Institute of Aeronautics and Astronautics. https://drive.google.com/drive/u/0/folders/1hOUyhr7jtv65HLhXofrR8VwvRt0HjL8d

Cetinsory E, Sirimogllu E, Oner K, Unel M. (2011). Design and development of a tilt-wing UAV. Turkish Journal of Electrical Engineering and Computer Sciences. (PDF) Design and development of a tilt-wing UAV (researchgate.net) (https://www.researchgate.net/publication/298957388_Design_and_development_of_a_tilt-wing_UAV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)

Keane A J, Sobester A, Scanlan J P. (2017). Small Unmanned Fixed-Wing Aircraft Design, A Practical Approach. Wiley. Small Unmanned Fixed-Wing Aircraft Design: A Practical Approach A. J. Keane et al.John Wiley and Sons, The Atrium, Southern Gate, Chichester, West Sussex, PO19 8SQ, UK. 2017. xl; 447pp. Illustrated £80.50. ISBN 978-1-119-40629-7. | The Aeronautical Journal | Cambridge Core (https://www.cambridge.org/core/journals/aeronautical-journal/article/small-unmanned-fixedwing-aircraft-design-a-practical-approach-a-j-keane-et-aljohn-wiley-a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)

# Appendix

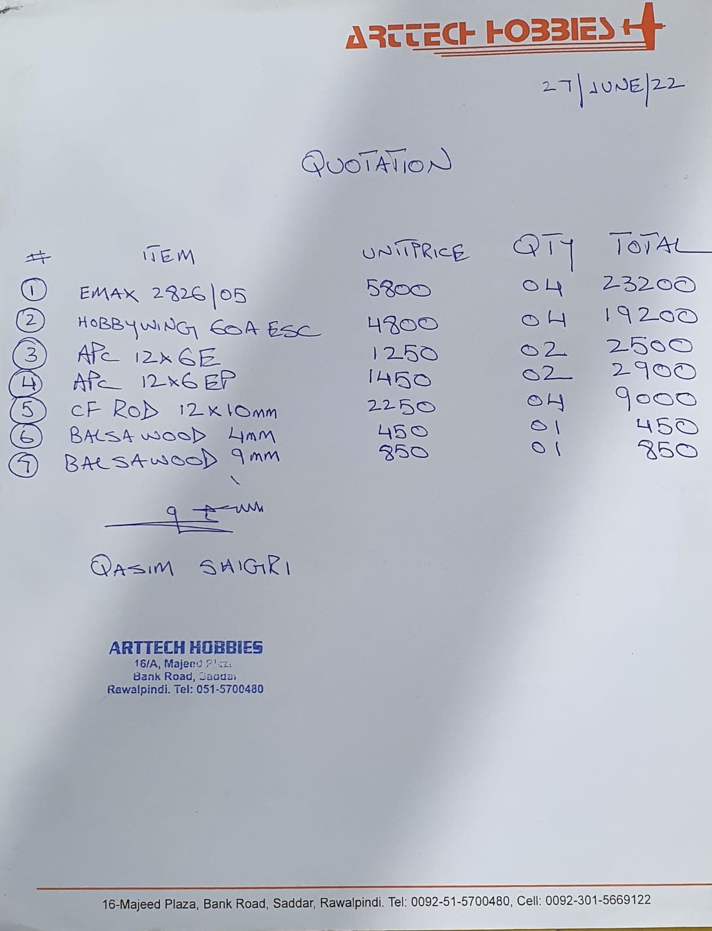
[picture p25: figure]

## A.1. Cost Quotations

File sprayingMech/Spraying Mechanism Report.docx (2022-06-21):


For given spray zone, multiple spraying approaches were considered and as a result of detailed Mathematical calculation & optimization, following spraying mechanism is finalized for drone

12V brushless water pump of max speed 3.5L/min, 1MPa pressure & max power of 40W is used. This pump uses 5A ESC and it is specially designed for agriculture drones.

Brushless pump enables variable flow rate which makes spraying mechanism more efficient as explained in Control System part.


This drone uses nozzles of two types: Brass nozzles in front wings create fine spray with 0.5mm outlet. Nozzles in rear wing create atomized mist of pesticide using 0.1mm outlet for spray to reach all parts of plants. Plastic pipes of 5mm diameter connect pump to nozzles on both wings.

The concept of multiple nozzle diameters is introduced in latest DJI Agras drones as a step to improve spray efficiency in small fruit trees where larger droplets cannot penetrate.

Brass nozzles are used since they are long-lasting, lightweight and cheap.

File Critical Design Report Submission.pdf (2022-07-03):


## Unmanned Aerial System (UAS) Challenge Pakistan 2022

### National University of Sciences and Technology

## Critical Design Report – The Hive

Team Members

Name | University | Major | Standing
Sarah Naeem – Team Lead | NUST H-12 | Mechanical Eng. | Sophomore
Jawad Akbar | NUST H-12 | Mechanical Eng. | Sophomore
Hamza Hussain | NUST H-12 | Mechanical Eng. | Sophomore
Syed Muhmmad Hassan Kazmi | NUST H-12 | Mechanical Eng. | Sophomore
Ahmed Bin Mushtaq | NUST H-12 | Electrical Eng. | Sophomore
Muhammad Hassaan Ghazali | NUST H-12 | Electrical Eng. | Sophomore
Ali Khalid | NUST H-12 | Electrical Eng. | Sophomore
Muhammad Saad Bin Tariq | NUST H-12 | Geo Informatics Eng. | Sophomore
Muhmmad Adeel | FAST NUCES -Isl | Computer Sci. | Sophomore
Syed Muaz Ashrafi | NUST -H12 | BS. Economics | Junior

Approved by Dr. Kashif Javed Assistant Professor at SMME NUST Faculty Supervisor – The Hive

Signature of Compiler – Sarah Naeem Team Lead – The Hive

## Table of Contents

Nomenclature | Error! Bookmark not defined.
1.1. Proposed Design | Error! Bookmark not defined.
1.2. Payload & Mission summary | Error! Bookmark not defined.
2. Project Management | Error! Bookmark not defined.
2.1. Progress Review | Error! Bookmark not defined.
2.2. Summary of Project Resources, Manufacturing and Risks | Error! Bookmark not defined.
4.1. Design Rationale | Error! Bookmark not defined.
4.1.1. Airframe | Error! Bookmark not defined.
4.1.1.1. Wings | Error! Bookmark not defined.
4.1.1.2. Empennage | Error! Bookmark not defined.
4.1.1.3. Fuselage | Error! Bookmark not defined.
4.1.1.4. Landing Gear | Error! Bookmark not defined.
4.1.2. Propulsions | Error! Bookmark not defined.
4.1.3. Control Surfaces | Error! Bookmark not defined.
4.1.3.1. Aileron sizing | Error! Bookmark not defined.
4.1.3.2. Rudder sizing | Error! Bookmark not defined.
4.1.8. Spraying Mechanism | Error! Bookmark not defined.
4.1.8.1. Spray Nozzle | Error! Bookmark not defined.
4.1.8.2. Micro Diaphragm Pump | Error! Bookmark not defined.
4.2. Aerodynamic Analysis | Error! Bookmark not defined.
4.2.1. Airfoil Analysis | Error! Bookmark not defined.
4.2.2. Wing And Fuselage Analysis | Error! Bookmark not defined.
4.2.3. Tail Analysis | Error! Bookmark not defined.
4.3. Structural Analysis | Error! Bookmark not defined.
4.4. Performance & Dynamic Analysis | Error! Bookmark not defined.
4.4.1. Vertical Flight | Error! Bookmark not defined.
4.4.1.1. Assumptions | Error! Bookmark not defined.
4.4.1.2. Mathematical Model | Error! Bookmark not defined.

4.4.2. Horizontal Flight | Error! Bookmark not defined.
4.4.3. Rotors Transition State | Error! Bookmark not defined.
4.4.3.1. Conventions | Error! Bookmark not defined.
4.4.3.2. Mathematical Model | Error! Bookmark not defined.
4.5. Weight Analysis | Error! Bookmark not defined.
4.6. Control System and Flight Controller | Error! Bookmark not defined.
4.6.1. Flight Controller Software | Error! Bookmark not defined.
4.6.2. Image Processing | Error! Bookmark not defined.
4.6.3. Path Optimization | Error! Bookmark not defined.
4.5. CAD Model | Error! Bookmark not defined.
5.1. Safety Steps in Control & Computing System Design: | Error! Bookmark not defined.
5.2. Safety Steps in Propulsion Design: | Error! Bookmark not defined.
5.3. Safety Steps in Spray System Design: | Error! Bookmark not defined.
6.2. Spray Tank | Error! Bookmark not defined.

## List of Figures

Figure 4.vertical stabilizer with labeled aileron variables.[9]

Figure 5. Extract from elevator characteristics for common aircrafts. [9]

Figure 6. Horizontal tail and elevator [9]

Figure 7. Vertical Tail and Rudder [9]

Figure 8. Extract from Characteristics of Rudder for several aircrafts [9]

Figure 24. Manufacturing process for spray tank. [12]

## List of Tables

## 1. Summary of CDR Report

### 1.1. Proposed Design

This novel design includes a quad tiltrotor fixed-wing UAV configuration with each rotor attached at the ends of the four wings. With a wingspan of 1.44m and a fuselage length of 1.55m, the UAV has a mass of 4 kg, with a capacity of 3kg for pesticide carriage. The maximum spraying capacity of the drone is 3.5L/min.
With a full payload, it can cruise at 15ms⁻¹
consuming only 84 Watts for propulsion. The drone can fly at 30ms⁻¹
(max. airspeed for the required mission) with rotors burning only 452 Watts. The UAV can achieve a 55ms⁻¹ airspeed (not employed in the current mission) with its 12.5kg maximum thrust.
The spraying mechanism includes two types of nozzles for spraying and misting to maximize spray quality and reduce pesticide consumption per acre. The pump has a BLDC motor for controllable flow and a maximum pressure of 1MPa at 40 Watts power consumption.
Selig S1210 & S1223 are used as front & rear wings airfoils giving the optimum lift-to-weight ratio of wings.
This report provides a thorough analysis and calculation of the drone's mission performance, manufacturability, procurement, and mitigation of all possible safety hazards. This UAV is capable of:
- Stable flight in vertical mode due to widely spaced rotors from the fuselage
- Powerful horizontal flight via thrust from all four rotors positioned horizontally
- Stable transition in flight modes due to variable tilting angles of rotors

Compared to typical fixed-wing and multi-rotor configurations, this configuration produces optimum results as an agriculture UAV for the required mission profile. Comparison with other configurations results in:

- 5.5 to 6 times more power efficient in horizontal cruise than multi-copters. i.e., suitable for spray zones far away from Ground Control Station (suitable for the longest route of 4km in mission)
- Higher precision in spraying than fixed-wing configuration due to capability of hovering, gliding, and staying at transition state while spraying
- More stable hovering and spraying than its parent configuration quad plane

Table 1. Summary chart for CDR

Team Name | The Hive
Review Items | Refer below to section 1.2.
Changes since PDR
Change | Reason
The High wing configuration is replaced with a mid-wing configuration. | Allows for easier to manufacture detachable wings and to reduce lift generation.
Aft conventional tail type is replaced with cruciform aft tail configuration. | Greater wake generation would negatively effect vertical stabilizer of conventional tail
TMotors MN5008 are replaced with EMAX GT-2826 KV860 | Tmotors are not available locally, and the team changed it to EMAX due to temporary import restrictions
6S Battery is replaced with 4S | EMAX GT-2826 KV860 requires a 4S Battery
Supervisor | Dr. Kashif Javed – Assistant Professor at SMME
Team Lead | Sarah Naeem

### 1.2. Payload & Mission summary

The UAV will carry the load at its maximum capacity, i.e., 3kg. It will follow the longest route of 4km towards the spraying zone at a cruise speed of 15ms⁻¹
, ideally consuming 266 seconds and 7.75Wh energy. The UAV will cover the complete spray zone in 118-125 seconds, following its optimal path for the least time consumption, consuming 32Wh energy. UAV will then cruise back to landing at 10.7ms⁻¹ ,
consuming 47 seconds and 0.65Wh energy. Hence, including 3 seconds of takeoff & 5 seconds of landing, and a transition time of 1.7 seconds, UAV will complete the mission in 441-455 seconds using the optimum energy consumption approach. It is adopted in this mission since time is not an issue and completing the mission before 10 minutes does not end up in bonus points. However, in real-world scenarios in an emergency, this UAV can complete the same mission in <290 seconds with only 28% more power consumption. Details are provided in the Engineering Analysis part.

### 2. Project Management

### 2.1. Progress Review

As the preliminary design review mentioned, the team is subdivided into groups for more accessible communication and effective workload distribution. The previous division has been revised since and is given in table 1.2

Table 2.1.1. Team Division and description

The workflow in Figure 2.1.2. shows task division from the PDR up to manufacturing and is divided according to the groups mentioned in Table 2.1.1.
A team tracker on the Google Drive Shared folder tracks the progress & timeline of each team till the CDR. Figure. b.b.b shows a part of The Hive Tracker.
All files in the project, including CAD models, reports, simulations, and source codes, are managed on Google Drive & GitHub repository [1] shown in Figures 2.1.3 & 2.1.4, respectively.

Moreover, the team conducted weekly joint team meetings, occasional team meetings with the faculty advisor and regular meetings of different groups to ensure timely completion of work and maintenance of the Project Progress tracker. Communication is done via MS Teams for meetings, WhatsApp groups for regular updates and Emails for notifications & announcements.

Sr # | Designation/subgroup | Name(s) | Assigned tasks and roles
3. | Mechanical design | • | Hamza Hussain
- Jawad Akbar
- Sarah Naeem
- Syed Muhammad Hassan
| | | Kazmi
- Aerodynamic Analysis
- Structural and stress analysis
- CAD model
- Airframe manufacturing and material selection
4. | Electrical Circuitry | • | Ali Khalid
- Muhammad Hassaan Ghazali
- Propulsion system design
- Electrical component selection
- Battery performance analysis
5. | Spraying Mechanism | • | Muhammad Saad bin Tariq | • | Spraying mechanism selection
- Selecting suitable pump, nozzles and supporting
| | | | | components
- Spray tank design and manufacturing
6. | Business Model | • | Syed Muaz Ashrafi | • | Outreach
- Industry support and collaboration
- Business model
7. | Control | & | Computing
System
- Ahmed bin Mushtaq
- Muhammad Adeel
- Control and computing system design
- Selecting supporting hardware


Figure 2.1.2. Project Workflow after PDR

Figure 2.1.3. Shared Google Drive Folder. [2] | Figure 2.1.4. Shared Google Drive Folder. [2]

### 2.2. Summary of Project Resources, Manufacturing and Risks

Project Part Human
Resource

Other
Resources

Procurement Manufacturing/ Development

Risks | Mitigation
Spraying Mechanism | Saad bin Tariq | None | Nozzles, Pump, Pipes and connectors | Optimized spray tank | Leakage, nozzle blockage, unavailable fluid to inflow. | Sump tank, nozzle filters and good connectors.
Flight Control System | Ahmad bin Mushtaq | ArduPilot source code, Pixhawk 2.4.8 | Open-source software + local available hardware | Fork the ardupilot repo and develop & compile firmware locally | Malfunctioning custom firmware | Continuous trial & error on in real-time flight
Computing System | Muhammad Adeel | Dronekit-python source code, Pytorch, Numpy | Open source | Fork the repo, develop according to needs and use them | Malfunctioning custom firmware | Continuous trial & error on in real-time flight
Aerodynamic Design | Jawad Akbar | ANSYS Fluent 2022 | NA | Design revaluation in case of unstable flight | Unfavorable lift/drag generated during flight. | Thorough CFD simulation and performance calculations.
Structure Design & Stress Analysis | Hamza Hussain Sarah Naeem | ANSYS Workbench | NA | Design revaluation in case of abnormal stress generation | Airframe damage. | Thorough calculations and appropriate manufacturing techniques
CAD model | Hamza Hussain Muhammad Hassan Kazmi Sarah Naeem | Solidworks 2022 | NA | NA | Improper dimensions used in model leading to errors in manufacturing | Thorough revaluation
Manufacturing | | CAD model, equipment | Raw material | Airframe, tank, supports | Material damage and injuries | Manufacturing under experienced personnel guidance.
Propulsion System Design | Muhammad Hassaan Ghazali | None | All hardware components | None | Faulty parts. Part damage & malfunction mid flight | Procurement from well known vendors. Proper connections.
Battery & Power distribution design | Ali Khalid | None | All components | None | Battery hazards | Employ safe battery practices.
Social Media Outreach & Busin ess Case | Muaz | Social media accounts. Graphic design software | None | None | Digital backlash. | Practice healthy cyber habits.

Table 2. Project resources, manufacturing, and risks

### 3. REQUIREMENT REVIEW

### 3.1. Mission Requirements and Verification

For table 4, the term ‘shall’ label a mandatory requirement and the term ‘should’ designates a highly desirable requirement.

Requirements | Verification
A detailed CAD assembly with emphasis on feasibility of design and manufacturing, control capacity and airworthiness. | Detailed CAD assembly created on Solidworks 2022 includes all components and structures employed in the final design.
UAS shall have either a fixed wing, rotary wing, or VTOL airframe configuration. | The design is tilt-rotor transition, fixed-wing VTOL aircraft
MTOM including payload and UAS shall not exceed 6.9 kg. | In weight analysis, the total mass with full payload is 6.9kg
UAS design should cater to rapid assembly/disassembly. | Easy to assemble airframe.
The UAS shall navigate waypoints and spray at targeted area in a fully autonomous manner and it should carry out fully autonomous take-off and landing. | Control & Computing System enable complete autonomy during take-off, spray & landing along with some advanced computing features.
The payload shall be a minimum of 500 ml. | There is 3L payload
The spray tank material should comply with UL 94, V0 flammability standards. It can be detachable or fixed to the UAV. For detachable tanks, re-attachment must be possible within the shortest amount of time. | Fixed spray tank manufactured from Carbon fiber is employed.
UAS airframe shall be designed from scratch. | Entire airframe is self-manufactured.
Cost for COTS components shall not exceed PKR 250,000. Proposed design solutions should be cost-efficient. | Total cost for COTS items adds up to 146K which is well below the specified limit.
Radio Equipment shall comply with PTA directives and licensed for use in Pakistan with a reliable operating range of 1km. Control of the UA and the FTS is ‘spread spectrum’ complaint to 100mW spread spectrum configuration to IR2030 and CE marked 4. | 433 MHz 500MW Telemetry used with range of 2.5km and spectrum available for personal/household devices
UA shall automatically return to landing zone/take-off or activate flight termination after a loss of data link of more than 30 seconds. | Advanced RTL feature in case of disconnected telemetry
UA shall automatically terminate flight in case of loss of GPS signal, for more than 3 minutes. | Flight termination feature included in the flight control system
‘Return Home’ signal shall be capable of activation by safety pilot. | Available in Mission Planner for Ground Control Station
A separate GPS data logger shall be fitted on top of the UAV, with clear exposure to the sky allowing real-time GPS information recording from take-off till landing. It shall also provide post-flight evaluation of the 3D trajectory. Placement of tracker should comply with vehicle safety and provide a glitch free flight safety review. | Provision has been left in design for GPS data logger and the control system is also compatible with it.
UAS design should plan on a target mission flight path with a distance of 2-4 km, from take-off to landing. | (With ref to battery consumption)
UAV to operate further than 500 m up to 1000 m where it may be flown safely and tracked within segregated airspace. | Telemetry used in UAV allows safe communication up to 2.5km range

UAV shall fly at a maximum altitude of 100m. | UAV is designed to cruise at about 30m AGL
UAV shall operate from within 10m x 30 m box, oriented at 30 degrees of wind direction. Landing must be within box, may be touchdown or roll out. | UAV shall use advanced computer vision to detect exact landing position and shall land with centimeters precision
Ground control station shall display all required information and be visible to operators, flight safety officers and judges. | Using telemetry, flight data logs are sent to ground control station using MAVlink and are displayed in mission planner
Should operate in winds of 20 kts gusting up to 25 kts and light rain. Shall be capable of landing and take-off in crosswind components to runway of 5 kts with gusts of 8 kts. | Drone shape designed for minimum air friction caused by wind High Thrust motors used for powerful propulsion against any windspeed below 55kts
Maximum airspeed in level flight shall not exceed 60 KIAS. | 35-40 KIAS adequate for completing the mission. Motor thrust will be adjusted accordingly.
Design and construction shall employ good design practice and use appropriate materials and components. | All materials and manufacturing methods are finalized after a thorough market analysis.
Design shall be supported by satisfactory structural integrity, stability and control, flight and navigation performance and reliability of critical systems. | Balsa airframe with carbon fiber reinforcements for structural integrity. Pixhawk, GPS and image processing for flight control and navigation.
Batteries used shall contain bright colors for easy detection in the event of a crash. | Battery pack will be bright colored.
At least 25% of upper, lower and each side shall be a bright color to facilitate visibility in air and event of a crash. | The entire external surface will employ surfacing of bright colored sheets.
UA shall remain within VLOS of remote pilot and remain below 100m AGL. | UAV path trajectory will make sure that it remains in boundaries
UA shall not be flown within 30 m of any person/structure not under the control of the Remote Pilot. During take-off and landing, it shall not be flown within a 10m distance. | UAV will not cruise below 30m in horizontal flight and would follow the exact trajectory where no humans intervene
UA shall remain in controlled flight and within the demonstration zone boundary during the entire flight | Safety precautions and settings are all set in flight control system
UA appearing uncontrolled or moving into ‘No Fly’ zone shall be subjected to manual override, failure to do so shall activate flight termination. | Safety precautions and settings are all set in flight control system
Consideration should be given to environmental impact. | BLDC motors with minimum noise production are used and environmentally friendly practices are employed for manufacturing.

Table 3. Requirement Review

### 3.2. Mission Success Criteria

The mission will be considered a success if the following criteria are met:

I. The UA covers the longest distance path to reach the SZ and navigate all WPs.
II. | The UA completes the entire mission within 10 minutes.
III. | The UA carries adequate payload to effectively spray entire spray zone.
IV. | The UA performs successful flight termination and manual override.
V. The UA performs controlled flight without any damage to itself, property, or people. VI. No safety violation occurs.

## 4. Design Description

### 4.1. Design Rationale

4.1.1. Airframe
A fixed-wing airframe design has opted for our UAV with a double pair of wings placed along the same axis. The wings are positioned midplane to the fuselage with a tilting rotor on each wing. This orientation provides the desired weight, strength, and performance efficiency in our mission objectives.
4.1.1.1. Wings
Our design includes two rectangular mid-wing pairs, placed one after the other, with a taper ratio of 1 and a dihedral angle of zero. The design follows a primary unswept wing with an aspect ratio of 7.2 (low aspect ratio). A lower aspect ratio allows for easier maneuverability which is one of the core requirements of our mission.[3]

The wingspan of both wings is approximately 1440 mm. The airfoil in the leading pair of wings is S1210[4], oriented at zero degrees. The trailing wings use S1223[5], oriented at five degrees. Each wing section has a chord length of 200 mm. The chosen orientation and dimensions provide us with the ideal amount of lift, cruising speed, and altitudes required for the fly-off mission. A skeletal structure composed of balsa cross-sections and longitudinal spars will provide the main frame of the wings. This frame is reinforced by high-strength and lightweight circular rods running along the entire wingspan. The frame is surfaced to provide a smooth, streamlined surface for good aerodynamic performance.

Each wing will house a 9 g servo and a 20 g servo for the ailerons and tilting rotors. Rubber pipes will also run along its length with the spray nozzle attached at one end and to the pump at the other. Balsa wood cross-sections are placed perpendicular to the longitudinal-lateral plane. These cross-sections will be manufactured to match the airfoil used. Provisions for support rods, servo motors, wiring, and spray system are provided in these cross-sections.

The wings can be detached from the main assembly through simple reinforced connections to allow rapid assembly/disassembly. The details for these connections are discussed extensively in the manufacturing portion.

4.1.1.2. Empennage
The Empennage refers to the tail section composed of a vertical and horizontal stabilizer. The UAV will ideally cruise at a zero-degree pitching angle at all times. The Sum of moments along all three axes must then always be zero. Due to the presence of 4 tilting rotors with relatively large propeller blades, a wake region will be generated. This wake must not blanket our tail sections, significantly reducing control efficiency. Our Empennage must also be lightweight and provide sufficient Control. For this, a cruciform tail orientation has been opted for. It is a type of aft tail configuration, intermediate between the conventional and T-tail, where the vertical and horizontal tails form a '+'. It combines the benefits of both and reduces several drawbacks of both tail configurations. [8] If aligned properly, a deep stall is avoided while maintaining low wing weight. Section 4.2. further shows calculations for the tailplane area. Control Surfaces are discussed ahead.
4.1.1.3. Fuselage
For finalizing the fuselage design, a fuselage design requirements verification rubric was employed. Table 2. summarizes the final optimized design.[6]

Table 4. Fuselage Design requirements and verification
4.1.1.4. Landing Gear
The landing gear is essential for safe takeoff and landing and, if designed well, can act as a shock absorber during crash landings. It must be made of appropriate material to avoid shock caused by harsh and crash landing from traveling through the Airframe. For our design, skids are selected as landing gears. These are fixed supports that are attached to the UAVs. These are widely used in VTOLs as there is no need for wheels. The design employs a four-piece landing gear in table-leg orientation. In this type, four rods are connected to the fuselage via hinges. The rods are fastened to one another via a rubber or elastic strip, resembling a table leg. The material chosen is carbon due to its lightweight and high-strength properties. In the event of a crash landing, the rubber material and the hinges provide a damping mechanism; hence, the material breaking chances are low. The landing gear will widen when the UAV lands, but the rubber provides a restoring force to limit this expansion. This action-reaction force pair causes damping and absorbs the shock that the UAV experiences. In case of a crash landing, only the components damaged are repaired or replaced. Unlike most landing gear systems, the entire assembly will not be replaced.
4.1.2. Propulsions
Power & Propulsion system of this UAV consists of following:
- 4 EMAX GT-2826 KV860 Brushless Motors
- 14*7’’ Carbon Fiber propellers
- Turnigy 5000mAh 4S Li-Po Battery with 40C Discharge Rate
- 20g servos for tilting individual rotors
These components are selected after extensive calculations for optimum performance in fly-off mission. Note: MN5008 mentioned in PDR is replaced by EMAX because it wasn’t locally available.
Design Requirement | Verification
Adequate space to house payload and system hardware. | The mounting plate runs through the entire length of the fuselage with a payload tank mounted between it. Sufficient free space remains after the assembly of all components.
Low weight. | A monocoque structure is employed using balsa wood bulkheads and reinforced longitudinal spars. It is covered using heat shrink iron-on model aircraft covering (7.7g/ sq. ft.).
It provides a sturdy mounting platform for landing gear. | The landing gear mounts are reinforced at the main mounting plate.
Generates the lowest drag possible. | Low wetted and side area with a streamlined nose and symmetric, streamlined contours result in minimum drag.
It maintains external symmetry. | It has an elliptic shape, symmetric about the longitudinal axis
Airworthiness and compatibility for flight during weather conditions are mentioned in mission requirements. | A sturdy airframe and high-strength iron-on covering are resistant to high winds & gusts and light rain (tensile strength 1,757 kg/sq cm [7]).
Manufacturing feasibility | Semi-monocoque structures have better manufacturability than monocoque designs with increased strength than truss assemblies. Locally available material and manufacturing methods are employed for easy access and guidance on equipment handling.
Structural Integrity and strength | Truss elements are employed where necessary, reinforced by balsa cross-sections along the longitudinal axis and interlinked support structures allowing loads to be distributed over the entire assembly.

Figure 1. Power as a function of Thrust

Figure 2. Thrust as a function of Power


Figure 3. EMAX GT2826/05 KV860 performance values

Data of all locally available motors is collected into the GitHub repository. The detailed datasheet of EMAX motors is not available online. All the data from the official website and thrust tests in workshops is gathered using finite values for this motor and datasheets available for similar motors; the closest continuous function was plotted against experimental values of thrust & power as shown in Fig. 4 & 5. Below are some power & thrust specifications of the motor used. Thrust for a single motor is written as a function of power using an online function calculator as:

tℎrust = −0.001632532 ∙ power² + 5.3238 ∙ power + 250 − − − (i)

This continuous function gives a precise value for power between 50-850 Watts. Lift & Drag values for the Airframe on different airspeeds were obtained from simulations (detail in aerodynamics section). Again, using finite values, the estimated function was plotted for both lift & drag against airspeed.

lift = 0.350317 ∙ v

2 − 0.202576 ∙ v | | − − − (ii)

drag = 0.0350823 ∙ v

2 + 0.00372739 ∙ v | − − − (iii) | ∴ v = airspeed

Cruise speed is calculated as: lift = 0.350317 ∙ v

2 − 0.202576 ∙ v = total mass of drone

Using this relation, the ideal cruise speed with a full payload, i.e., 6.9kg (flight towards Spray Zone), comes out to be 14.2ms⁻¹
, and cruise speed without payload, i.e., 3.9kg (flight back to landing), comes out to be 10.7ms⁻¹

Power consumption is calculated as:

drag = 0.0350823 ∙ v

2 + 0.00372739 ∙ v = tℎrust of propulsion system

The thrust required for a total payload comes out to be 0.727237 kgf (0.181809 kgf for each motor). Power consumed to require this thrust is calculated by eq. (i) It comes out to be 84.5723W (21.143W per motor). Similarly, the thrust required without payload is 0.421658 kgf, and power consumption is 47.8332W. Calculating energy consumption & time taken for ideal cruise flight of 4km from take-off to spray zone and 500m from spray zone to landing:

time =

4000m
14.2ms⁻¹ +

500m
10.7ms⁻¹ = 328.42s (Approx. 52
| | 1 minutes)
energy = 84.5723W ∙ 281.7s + 47.8332W ∙ 46.7s ≈ 7.2383 Wℎ | (< 10% of available battery)

Ideal time & energy consumption calculations for takeoff, transition, spray zone & landing were done. Calculations are too complicated to be added in CDR. Results are given below.

The battery's energy capacity is 74Wh, about 160% of the total power used in-flight via a 4km route


Figure 4. The calculation for Optimum Energy Consumption | Figure 5. The calculation for Optimum Mission Time

4.1.3. Control Surfaces
Controllability is a crucial characteristic of aircraft design. Control is defined as switching from one trim point to another, where trim refers to the state where the summation of forces along all three axes in an aircraft is zero. Control surfaces are employed to achieve controllability. Our UAV design employs the three primary control surfaces; ailerons, rudder and elevator.
4.1.3.1. Aileron sizing

Two parameters of the aileron, namely the
chord length (CA) and total length along the wing (ba/2) will be considered here. A statistical approach has been employed to find the dimensions of the
aileron.

Although many factors influence the chord


length of the aileron, one notable consideration is the distance of the rear spar from the trailing edge. The rear spar can serve as a hinge for the aileron, simplifying the design.

In the selected wing airframe, the rear spar is located 0.11 m away from the trailing edge of the wing. The total chord length of the wing is 0.2 m.

C = 0.2 m

As per the placement of the rear spar:

CA = 0.11 m [10]

CA/C = 0.55

Now by:
bA
b

=

CA
C

∴ b = 0.61 × 2 = 1.22

For either side: | bA/2 = 0.3355 m [10]

To avoid flow separation, maximum aileron deflection δA (positive and negative) will be set at 20 degrees.

Elevator design:; the one selected for the UAV.

The values for surface area and chord length ratios have
been selected from the following table for the Cessna 182 due to its smaller size and similar tail geometry to

The length of the elevator has been taken equal to the chord length of the horizontal stabilizer, that is:

bE = 0.18 m Cℎord lengtℎ of stablizer Cℎ = 0.18 m => CE = 0.44 × 0.18

Figure 4.vertical stabilizer with labeled aileron variables.[9]

Figure 6. Horizontal tail and elevator [9] Figure 5. Extract from elevator characteristics for common aircrafts. [9]

CE = 0.079 m | ∴ CE/Cℎ = 0.44
4.1.3.2. Rudder sizing

Figure 7. Vertical Tail and Rudder [9]

Rudder sizing follows a similar approach. A rectangular rudder has been selected for the design. In the design,
bv = 0.188 m bR = 0.188 m[10]

Figure 8. Extract from Characteristics of Rudder for several aircrafts [9]

Now,
CR
CV
= 0.42, | CV = 0.18 m | => | CR = 0.18 × 0.42 = 0.0756 m [10]
4.1.8. Spraying Mechanism
4.1.8.1. Spray Nozzle
Four nozzles will be used at either end of the wings. Nozzles extrude from the wing for easy cleaning and will be connected using 5mm rubber pipes. In addition, connectors will be used for easy and secure connection of the pipes since the wings are detachable; hence, 4 connectors in each wing will ensure no leakage. The pump and the tank will be placed in the fuselage for efficient weight distribution. The nozzle chosen can operate in spray mode and mist mode, providing efficient coverage for the spray zone.
4.1.8.2. Micro Diaphragm Pump

A brushless pump is chosen for this mission. The performance details for this model are listed in Table 5. Lightweight and high quality were the main selection criteria for the pump.
Caution: Pump should be used in dry condition, cannot submerge into water.
Nozzle Material | Copper | Spray Distance | 1 meter (can be varied)
Spray Flow | 0.2-0.7 ltr/min | Pipe Diameter | 5 mm

Table 5. Spray Nozzle specifications.

Voltage | 12 V | Current | 3 A
Flow | 5ltrs/min | Power | 60 W
Pressure | 100 Psi | Connector Size | Fits 6-10 mm inner diameter pipe.

Table 6. Pump specifications

### 4.2. Aerodynamic Analysis

4.2.1. Airfoil Analysis
I Initially, airfoils generating high lift and low Reynolds numbers were short-listed to cope with the mission and efficiency constraints. After an iterative process of combining two airfoils, the best possible combination was selected. The lift curve was obtained using Xfoil. With an upstream airfoil S1210 at 0 pitch, a downstream airfoil S1223 at 5 pitch, a chord length of 200mm for both airfoils and 0.49m between the wings gave a net lift coefficient of 2.43 for Reynold's number of 1.5-2 ×10⁵


4.2.2. Wing And Fuselage Analysis


With a maximum required force of 6.9kg during level flight the wing area was calculated using

A =

2Fl
ρV²Cl

The shape of the fuselage was kept elliptical to encourage laminar flow over the surface and wing edges, treating it as a streamline body during horizontal cruise. Also, considering it as a blunt body during VTOL

and transition state, the elliptical shape reduces pressure drag during vertical flight at much lower velocity


than cruise velocity. The nose was kept relatively long to make it sleek and streamline for reduced drag having 254mm length. The fuselage, nose and tail were kept symmetrical about the X and Z axis to avoid any lift generation. The following CAD model was generated for simulation. Simulation was carried out in Ansys® Fluent. The K-Omega turbulence model was opted and a tetrahedral mesh with average mesh size of 50mm and 5mm at fluid and surface zones respectively. [11]

Figure 10. CFD lift force values. | Figure 9. Velocity contour from CFD Analysis for chosen airfoil configuration.
Figure 11. Model Used for 3D CFD simulation. | Figure 12.Pressure contour from CFD simulation of test model.

Figure Figure 13. CFD results for forces along x 14. CFD for forces along y-axis (lift). -axis (drag).

4.2.3. Tail Analysis

The Volume Ratio model is used to compute the tail area. The tail should be sized to generate enough counter torque for adequate stabilization. Reasonable amendments were made to incorporate our design parameters and variation.

CHT =

SHT ∗ LHT

SW ∗ cMAC

; CVT =

SVT ∗ lVT
SW ∗ b

The values for the volume ratio of horizontal and vertical stabilizers were obtained from the tabulated data in Empennage Statistics and Sizing Methods for Dorsal Fins [8]. The Raymer and Roskam models were used for horizontal and vertical tails, respectively.

The results are concluded that the vertical tail sweeps from 200mm to 160mm chord having a mean chord length of 180mm meters and a height of 188mm. The horizontal tail has a 180mm chord and 820mm span. The horizontal tail is situated midway onto the vertical stabilizer to heighten it and prevent turbulent air from the propeller from disturbing its laminar flow. The aerodynamic center is situated 23.5" from the nose tip.

### 4.3. Structural Analysis

Bending Moment of wings:

Centre of mass along x = 46.2 mm

Total weigℎt of UAV = 6.9kg × 9.8

m
s

2 = 67.7N

Previously calculated lift force = 74 N

rear wing weigℎt = Wwing,rear = 160.45g = 0.16045kg

front wing weigℎt = Wwing,front = 153.96g = 0.15396kg

Assuming that each wing produces 1/4th of the total lift (L). Then the balance of vertical forces for the wings imply:

Front: (For lift=weight of UAV)

V =

L
4

− Wwing,front

V = (

67.7
4

) − (0.15396 × 9.8)

V = 25.54 N

Corresponding bending moment for center of mass at 0.0462 m:
W = 0.0462 × 25.54

W = 1.18 Nm

(For calculated lift)

V =

L
4

− Wwing,front

V = 17 N

Corresponding bending moment for center of mass at 0.0462 m:

W = 0.0462 × 17 = 0.785 Nm

Rear: (For lift=weight of UAV)

V =

L
4

− Wwing,rear

V = 15.35 N

Figure 15. Airfoil Section from wing CAD model.

Corresponding bending moment for center of mass at 0.0462 m:

W = 0.0462 × 15.35 = 0.71 Nm

(For calculated lift)

V =

L
4

− Wwing,rear

V = 16.93 N

Corresponding bending moment for center of mass at 0.0462 m:

W = 0.0462 × 16.93 = 0.78 Nm

### 4.4. Performance & Dynamic Analysis

4.4.1. Vertical Flight
4.4.1.1. Assumptions
- The UAV experiences negligible friction (drag) in the vertical direction
4.4.1.2. Mathematical Model

For vertical flight, the model is the simplest since drag is neglected. The real-life values will be significantly different, but since only takeoff and landing is vertical, there would be a negligible effect on overall mission time and energy consumption.

Summing all force vectors on UAV, ma = vertical tℎrust − weigℎt => a =

tℎrust−weigℎt
mass of UAV

Acceleration can be written as a power
function using the estimated function (thrust as a function of power). Distance traveled can be expressed as a function of total energy consumed, integrating it twice w.r.t time. Optimizing the total energy, we find out that 10.5kgf total thrust for the UAV gives optimum energy consumption for 30m takeoff
4.4.2. Horizontal Flight

For horizontal flight, calculations are simple too. Since the UAV is cruising at constant airspeed and altitude, all vertical components are of no concern; for horizontal components, drag = tℎrust.

Since lift can be expressed as a function of velocity using Fluent Simulations, velocity from lift = weigℎt comes out to be 14.2ms⁻¹
. From this cruise speed, drag can be calculated; hence, the required thrust is calculated using that drag. Since power can be written as a close function of thrust for EMAX GT-2826/5, power consumed can be calculated for the horizontal cruise. Using this methodology, power consumed during the cruise becomes 84 Watts.


Table 8. Horizontal Flight performance.

Table 7. Vertical Flight Energy consumption

4.4.3. Rotors Transition State
4.4.3.1. Conventions
- Tilt angle in horizontal flight is set as 0o and in vertical flight as 90o .
4.4.3.2. Mathematical Model

For simplicity, we assume that thrust magnitude
during the transition phase remains constant and only the tilt angle changes. The thrust provided by rotors is divided into vertical and horizontal components depending on the instantaneous tilt angle.

Vetical Tℎrust = Weigℎt − lift = Tℎrust ∙ sinθ => θ = sin⁻¹ (

Weigℎt − lift
Tℎrust | ) − − − (i)
Horizontal Tℎrust − drag = ma | => a =

Tℎrust ∙ cosθ − drag
mass of UAV − − − (ii)

Acceleration of UAV is represented as function of tilt angle & drag force. Tilt angle is a function of lift in (i). Fluent simulations show that drag & lift can be written as function of horizontal velocity as:

drag = 0.350317v

2 − 0.202576v − − − (iii) lift = 0.0350823v

2 + 0.00372739v − − − (iv)

Hence, using (i) and (iv), θ can be written as function of velocity.

θ = sin⁻¹ (
Weigℎt − 0.0350823v

2 + 0.00372739v
Tℎrust | ) − − − (v)

Using (ii), (iii) & (v), acceleration is written as function of velocity. Hence, equation becomes:

a =

Tℎrust ∙ cos (sin⁻¹ (

Weigℎt − 0.0350823v

2 + 0.00372739v
Tℎrust | )) − drag
mass of UAV | − − − (vi)
Velocity & Speed are given as: | v = ∫ a

t
t0

dt − − − (vii) distance s = ∫ v

t
t0

dt − − − (viii)

The flight controller does not continuously control tilting but controls discretely, i.e., changing every clock cycle, which changes the tilt angle every micro-second according to the equations above.

The easiest and most accurate way to calculate the complete spectrum of tilt angle, horizontal & vertical speed, lift, and drag is to distribute the time domain into discrete parts of microseconds (Δt) and then, from t = 0s & v = 0ms⁻¹
, start calculating lift, drag and acceleration. Use vi+1 = vi + aiΔt − − − (ix) & si = viΔt +

1
2

aiΔt

2
to calculate distance and next interval velocity.

Table 9. Vector Diagram for Transition state forces.

Calculations for the transition region are made in an excel sheet using this approach, keeping Δt = 20µs.


Table 10. Transition state performance values.

During the transition from 90o
to 0

o
, the time taken is 925ms and the distance covered is 6.3m.

Note: This calculation assumes that drone acceleration is the bottleneck, not the tilting servo speed because the tilting servo used in this UAV has a higher angular velocity than the transition state.


Figure 17. Thrust variation over time.

### 4.5. Weight Analysis

Weight analysis showed that the combined weight of the UAV and all its components minus the payload is approximately 3.9 kg, leaving behind a 3 kg capacity for payload, which is the ideal amount of fluid required for effective spraying of the entire spray zone. The weight analysis is given in the table below.


Table 11. Weight Breakdown

Figure 16. Drag and velocity variation over time.
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

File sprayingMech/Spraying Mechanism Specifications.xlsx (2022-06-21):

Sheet: Brushless Pump
Mini Brushless Water Pump
 | Type | Brushless Water Pump
 | Voltage | 12V
 | Max. Current | 3.5A
 | Max. Pressure | 1MPa
 | Dimensions | 160 x 100 x 60 mm
 | Max. Flow Rate | 3.5L/min
 | Weight | 350g

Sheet: Brass Nozzle
Brass Misting Nozzles
 | Type | Brass Fixed Mist Nozzle
 | Pressure | 20-70 kg / sq. cm
 | Flow Rate | 80-145 ml/min
 | Nozzle Diameter | 0.1 mm / 0.5 mm

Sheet: ESC
Spray Pump ESC
 | Voltage | 12V
 | Current Capacity | 5.5A

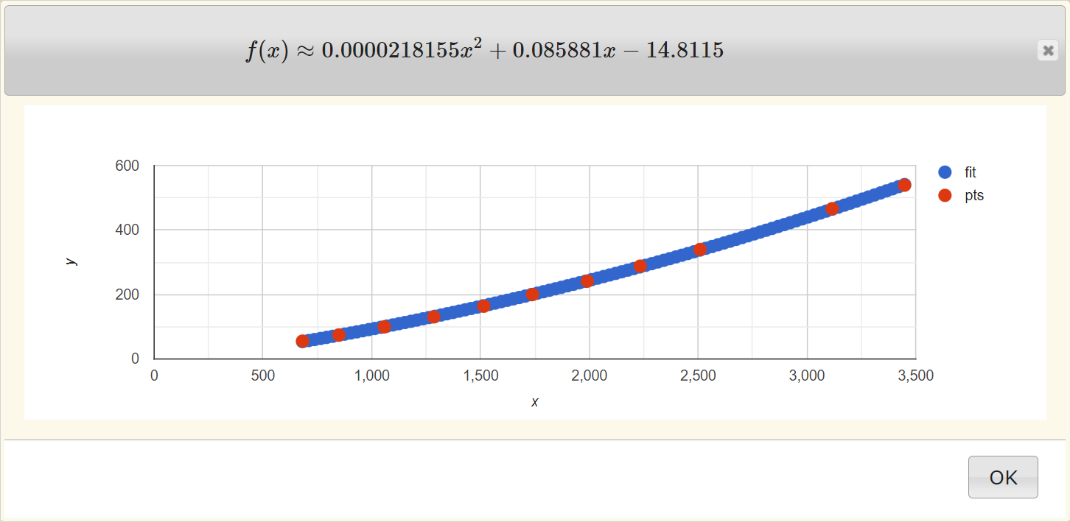
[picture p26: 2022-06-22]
Power & Propulsion System/MN5008 KV170 P17 5.8 power function.png

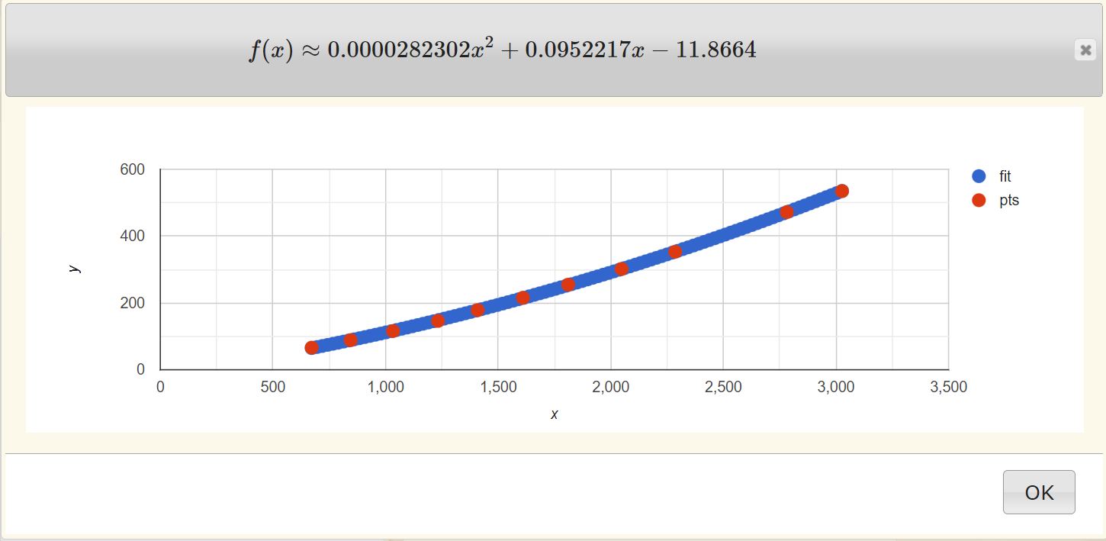
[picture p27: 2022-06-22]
Power & Propulsion System/MN5008 KV400 P15 5 power function.png

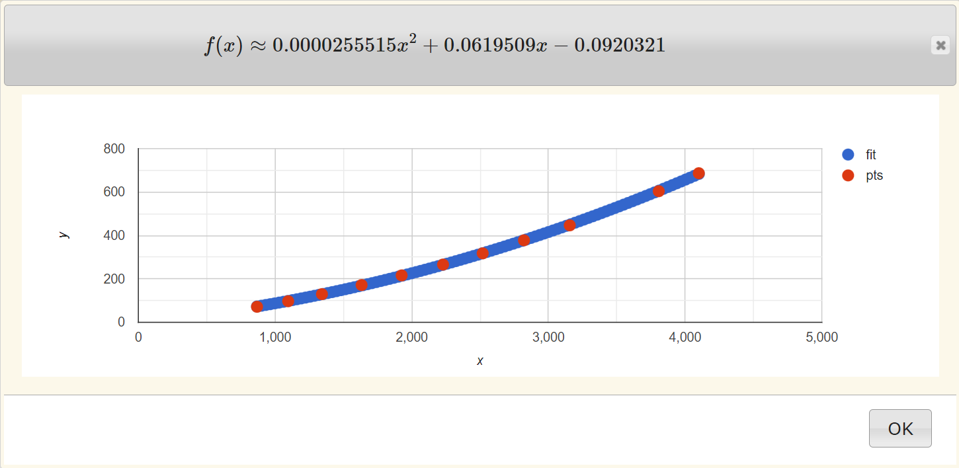
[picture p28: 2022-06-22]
Power & Propulsion System/MN5008 KV170 P18 6.1 power function.png

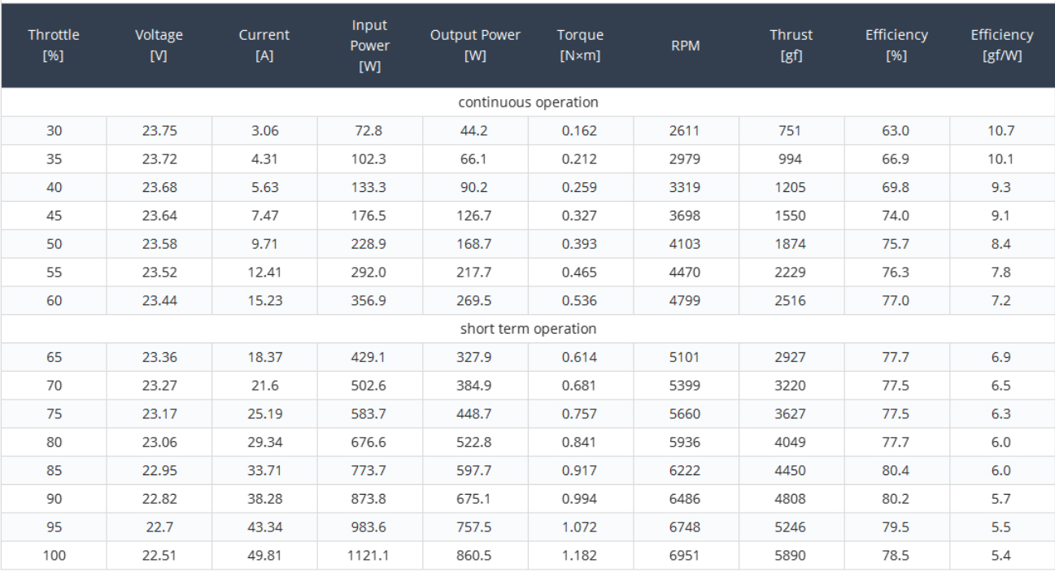
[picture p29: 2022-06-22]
Power & Propulsion System/MAD 5015.png

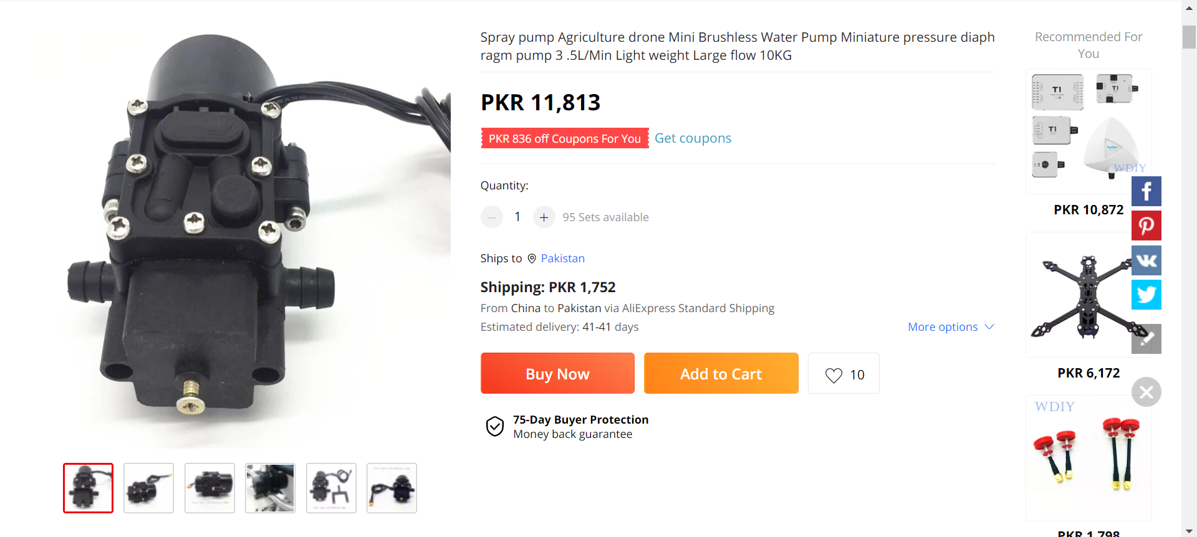
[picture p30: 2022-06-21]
sprayingMech/Pump 03.png

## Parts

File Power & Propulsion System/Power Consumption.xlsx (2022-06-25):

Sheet: Motors
Motor | Propeller | Voltage (V) | Current (A) | Power (W) | Thrust (g) | Efficiency (g/W)
MN5008 KV170 | Tmotors P17*5.8'' CF | 47.41 | 1.17 | 55.4697 | 682 | 12.29500069
 |  | 47.39 | 1.57 | 74.4023 | 849 | 11.41093757
 |  | 47.36 | 2.1 | 99.456 | 1058 | 10.63787001
 |  | 47.34 | 2.76 | 130.6584 | 1285 | 9.834805875
 |  | 47.31 | 3.46 | 163.6926 | 1515 | 9.255152646
 |  | 47.28 | 4.23 | 199.9944 | 1739 | 8.695243467
 |  | 47.24 | 5.11 | 241.3964 | 1991 | 8.247844624
 |  | 47.21 | 6.1 | 287.981 | 2234 | 7.757456221
 |  | 47.17 | 7.2 | 339.624 | 2509 | 7.387581561
 |  | 47.08 | 9.9 | 466.092 | 3116 | 6.685375419
 |  | 47.03 | 11.46 | 538.9638 | 3449 | 6.399316615
 | Tmotors P18*6.1'' CF | 47.39 | 1.51 | 71.5589 | 868 | 12.12986784
 |  | 47.37 | 2.05 | 97.1085 | 1096 | 11.28634466
 |  | 47.34 | 2.74 | 129.7116 | 1343 | 10.3537386
 |  | 47.3 | 3.63 | 171.699 | 1633 | 9.510829999
 |  | 47.27 | 4.57 | 216.0239 | 1926 | 8.915680163
 |  | 47.23 | 5.63 | 265.9049 | 2229 | 8.38269622
 |  | 47.19 | 6.73 | 317.5887 | 2519 | 7.931642404
 |  | 47.15 | 8.01 | 377.6715 | 2821 | 7.469454274
 |  | 47.1 | 9.48 | 446.508 | 3156 | 7.068182429
 |  | 46.99 | 12.85 | 603.8215 | 3807 | 6.304843402
 |  | 46.94 | 14.63 | 686.7322 | 4100 | 5.970303999
MN5008 KV340 | Tmotors P17*5.8'' CF | 23.47 | 2.88 | 67.5936 | 776 | 11.48037684
 |  | 23.43 | 3.98 | 93.2514 | 986 | 10.5735678
 |  | 23.38 | 5.33 | 124.6154 | 1224 | 9.82222101
 |  | 23.33 | 6.86 | 160.0438 | 1455 | 9.091261267
 |  | 23.27 | 8.53 | 198.4931 | 1697 | 8.549415572
 |  | 23.21 | 10.38 | 240.9198 | 1936 | 8.035869198
 |  | 23.15 | 12.4 | 287.06 | 2176 | 7.580296802
 |  | 23.08 | 14.71 | 339.5068 | 2440 | 7.186895815
 |  | 23 | 17.16 | 394.68 | 2701 | 6.8435188
 |  | 22.82 | 23.18 | 528.9676 | 3277 | 6.195086429
 |  | 22.72 | 26.39 | 599.5808 | 3556 | 5.930810326
 | Tmotors P18*6.1'' CF | 23.44 | 3.76 | 88.1344 | 996 | 11.30092223
 |  | 23.39 | 5.12 | 119.7568 | 1238 | 10.33761757
 |  | 23.33 | 6.93 | 161.6769 | 1541 | 9.531355438
 |  | 23.26 | 8.95 | 208.177 | 1822 | 8.752167627
 |  | 23.19 | 11.12 | 257.8728 | 2120 | 8.221107461
 |  | 23.11 | 13.46 | 311.0606 | 2394 | 7.696249541
 |  | 23.04 | 16.01 | 368.8704 | 2675 | 7.251869491
 |  | 22.95 | 18.83 | 432.1485 | 2966 | 6.863381453
 |  | 22.86 | 22.02 | 503.3772 | 3262 | 6.480229935
 |  | 22.63 | 29.46 | 666.6798 | 3909 | 5.863384491
 |  | 22.51 | 33.5 | 754.085 | 4215 | 5.589555554
MN5008 KV400 | Tmotors P15*5'' CF | 23.48 | 2.82 | 66.2136 | 672 | 10.14897242
 |  | 23.44 | 3.78 | 88.6032 | 845 | 9.536901602
 |  | 23.4 | 4.95 | 115.83 | 1033 | 8.918242252
 |  | 23.35 | 6.26 | 146.171 | 1233 | 8.435325749
 |  | 23.3 | 7.66 | 178.478 | 1409 | 7.894530418
 |  | 23.25 | 9.26 | 215.295 | 1610 | 7.478111429
 |  | 23.19 | 10.98 | 254.6262 | 1811 | 7.112386706
 |  | 23.13 | 13.04 | 301.6152 | 2048 | 6.790108721
 |  | 23.06 | 15.31 | 353.0486 | 2286 | 6.475029217
 |  | 22.9 | 20.6 | 471.74 | 2782 | 5.897316318
 |  | 22.81 | 23.44 | 534.6664 | 3027 | 5.661474145
 | Tmotors P16*5.4'' CF | 23.46 | 3.22 | 75.5412 | 803 | 10.62996087
 |  | 23.41 | 4.46 | 104.4086 | 1021 | 9.778887946
 |  | 23.36 | 5.93 | 138.5248 | 1259 | 9.088625286
 |  | 23.31 | 7.54 | 175.7574 | 1492 | 8.488974006
 |  | 23.25 | 9.28 | 215.76 | 1722 | 7.9810901
 |  | 23.19 | 11.19 | 259.4961 | 1956 | 7.537685537
 |  | 23.13 | 13.16 | 304.3908 | 2185 | 7.178272142
 |  | 23.05 | 15.66 | 360.963 | 2458 | 6.809562199
 |  | 22.96 | 18.53 | 425.4488 | 2750 | 6.463762502
 |  | 22.77 | 24.84 | 565.6068 | 3323 | 5.875106169
 |  | 22.67 | 28.16 | 638.3872 | 3591 | 5.625112784
 | Tmotors P17*5.8'' CF | 23.44 | 3.71 | 86.9624 | 917 | 10.54478717
 |  | 23.39 | 5.18 | 121.1602 | 1170 | 9.65663642
 |  | 23.33 | 6.99 | 163.0767 | 1447 | 8.873125345
 |  | 23.26 | 8.88 | 206.5488 | 1712 | 8.288598142
 |  | 23.2 | 10.92 | 253.344 | 1963 | 7.748357964
 |  | 23.13 | 13.17 | 304.6221 | 2230 | 7.320545686
 |  | 23.05 | 15.72 | 362.346 | 2491 | 6.874644677
 |  | 22.97 | 18.31 | 420.5807 | 2757 | 6.555222339
 |  | 22.87 | 21.65 | 495.1355 | 3090 | 6.240715925
 |  | 22.65 | 28.93 | 655.2645 | 3697 | 5.641996476
 |  | 22.53 | 32.83 | 739.6599 | 3982 | 5.383555334
EMAX GT2826/05 KV860 | P14*7'' | 15.6 | 7.06 | 110.136 | 795 | 7.218348224
 |  | 15.43 | 13.8 | 212.934 | 1283 | 6.025341186
 |  | 15.21 | 24.9 | 378.729 | 2021 | 5.33626947
 |  | 14.93 | 33.05 | 493.4365 | 2487 | 5.040162209
 |  | 14.68 | 41 | 601.88 | 2852 | 4.738486077
 |  | 14.47 | 57.3 | 829.131 | 3680 | 4.438381872

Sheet: D & L
Airspeed (m/s) | Lift (N) | Drag (N) | Lift (N) | Drag (N)
0 | 0 | 0 | 0 | 0
4 | 4.8773724 | 0.56971285 | 4.794768 | 0.57622636
8 | 20.819826 | 2.273879 | 20.79968 | 2.27508632
12 | 47.994604 | 5.0977856 | 48.014736 | 5.09657988
16 | 86.491328 | 9.036845 | 86.439936 | 9.04070704
20 |  |  | 136.07528 | 14.1074678
24 |  |  | 196.920768 | 20.29686216
28 |  |  | 268.9764 | 27.60889012
32 |  |  | 352.242176 | 36.04355168
36 |  |  | 446.718096 | 45.60084684
40 |  |  | 552.40416 | 56.2807756
44 |  |  | 669.300368 | 68.08333796
48 |  |  | 797.40672 | 81.00853392
52 |  |  | 936.723216 | 95.05636348
56 |  |  | 1087.249856 | 110.2268266
60 |  |  | 1248.98664 | 126.5199234
64 |  |  | 1421.933568 | 143.9356538
68 |  |  | 1606.09064 | 162.4740177
72 |  |  | 1801.457856 | 182.1350153

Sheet: Cruise
Speed | Vertical Thrust (kgf) | Horizontal Thrust (kgf) | Total Thrust (kgf) | Thrust per motor (kgf) | Power per Motor (W) | Total Power (W) | Cruise Efficiency
0 | 3.9 | 0 | 3.9 | 0.975 | 142.2583827 | 569.0335307 | #DIV/0!
0.1 | 3.901709636 | 7.383285714e-05 | 3.901709636 | 0.9754274091 | 142.3363092 | 569.3452369 | 1423.363092
0.2 | 3.902704339 | 0.0002192622449 | 3.902704345 | 0.9756760862 | 142.3816551 | 569.5266203 | 711.9082753 | Mass (kg) | 3.9
0.3 | 3.902984109 | 0.0004362881633 | 3.902984134 | 0.9757460334 | 142.3944106 | 569.5776426 | 474.6480355
0.4 | 3.902548947 | 0.0007249106122 | 3.902549014 | 0.9756372536 | 142.3745737 | 569.4982948 | 355.9364342
0.5 | 3.901398852 | 0.001085129592 | 3.901399003 | 0.9753497507 | 142.3221493 | 569.2885972 | 284.6442986
0.6 | 3.899533824 | 0.001516945102 | 3.89953412 | 0.9748835299 | 142.2371499 | 568.9485994 | 237.0619164
0.7 | 3.896953864 | 0.002020357143 | 3.896954388 | 0.974238597 | 142.1195951 | 568.4783805 | 203.0279931
0.8 | 3.893658971 | 0.002595365714 | 3.893659836 | 0.9734149591 | 141.9695122 | 567.878049 | 177.4618903
0.9 | 3.889649146 | 0.003241970816 | 3.889650497 | 0.9724126242 | 141.7869356 | 567.1477424 | 157.5410396
1 | 3.884924388 | 0.003960172449 | 3.884926406 | 0.9712316015 | 141.571907 | 566.2876281 | 141.571907
1.1 | 3.879484697 | 0.004749970612 | 3.879487605 | 0.9698719012 | 141.3244756 | 565.2979024 | 128.476796
1.2 | 3.873330073 | 0.005611365306 | 3.873334138 | 0.9683335345 | 141.0446978 | 564.1787913 | 117.5372482
1.3 | 3.866460517 | 0.006544356531 | 3.866466056 | 0.966616514 | 140.7326375 | 562.9305501 | 108.255875
1.4 | 3.858876029 | 0.007548944286 | 3.858883412 | 0.9647208531 | 140.3883659 | 561.5534635 | 100.2774042
1.5 | 3.850576607 | 0.008625128571 | 3.850586267 | 0.9626465668 | 140.0119614 | 560.0478458 | 93.34130763
1.6 | 3.841562253 | 0.009772909388 | 3.841574684 | 0.960393671 | 139.6035101 | 558.4140405 | 87.25219383
1.7 | 3.831832966 | 0.01099228673 | 3.831848733 | 0.9579621832 | 139.1631052 | 556.6524209 | 81.86065013
1.8 | 3.821388747 | 0.01228326061 | 3.821408488 | 0.9553521221 | 138.6908473 | 554.7633894 | 77.05047075
1.9 | 3.810229595 | 0.01364583102 | 3.81025403 | 0.9525635075 | 138.1868445 | 552.7473782 | 72.72991818
2 | 3.79835551 | 0.01507999796 | 3.798385445 | 0.9495963612 | 137.6512122 | 550.604849 | 68.82560612
2.1 | 3.785766493 | 0.01658576143 | 3.785802824 | 0.9464507061 | 137.0840732 | 548.336293 | 65.27813012
2.2 | 3.772462543 | 0.01816312143 | 3.772506267 | 0.9431265668 | 136.4855578 | 545.9422311 | 62.03888989
2.3 | 3.75844366 | 0.01981207796 | 3.758495878 | 0.9396239695 | 135.8558034 | 543.4232136 | 59.06774061
2.4 | 3.743709845 | 0.02153263102 | 3.743771769 | 0.9359429422 | 135.1949552 | 540.7798209 | 56.33123134
2.5 | 3.728261097 | 0.02332478061 | 3.728334059 | 0.9320835146 | 134.5031657 | 538.0126627 | 53.80126627
2.6 | 3.712097416 | 0.02518852673 | 3.712182874 | 0.9280457185 | 133.7805946 | 535.1223785 | 51.45407486
2.7 | 3.695218803 | 0.02712386939 | 3.69531835 | 0.9238295875 | 133.0274095 | 532.1096378 | 49.26941091
2.8 | 3.677625257 | 0.02913080857 | 3.677740629 | 0.9194351573 | 132.243785 | 528.9751398 | 47.2299232
2.9 | 3.659316779 | 0.03120934429 | 3.659449864 | 0.9148624661 | 131.4299034 | 525.7196136 | 45.32065634
3 | 3.640293367 | 0.03335947653 | 3.640446216 | 0.9101115541 | 130.5859545 | 522.3438182 | 43.52865152
3.1 | 3.620555023 | 0.03558120531 | 3.620729857 | 0.9051824643 | 129.7121357 | 518.8485427 | 41.84262441
3.2 | 3.600101747 | 0.03787453061 | 3.600300969 | 0.9000752423 | 128.8086515 | 515.2346062 | 40.25270361
3.3 | 3.578933538 | 0.04023945245 | 3.579159745 | 0.8947899363 | 127.8757145 | 511.5028579 | 38.75021651
3.4 | 3.557050396 | 0.04267597082 | 3.557306391 | 0.8893265977 | 126.9135444 | 507.6541775 | 37.32751305
3.5 | 3.534452321 | 0.04518408571 | 3.534741124 | 0.883685281 | 125.9223686 | 503.6894745 | 35.97781961
3.6 | 3.511139314 | 0.04776379714 | 3.511464177 | 0.8778660442 | 124.9024223 | 499.6096894 | 34.69511732
3.7 | 3.487111374 | 0.0504151051 | 3.487475795 | 0.8718689488 | 123.8539482 | 495.4157927 | 33.47404005
3.8 | 3.462368502 | 0.05313800959 | 3.462776241 | 0.8656940601 | 122.7771964 | 491.1087857 | 32.30978854
3.9 | 3.436910697 | 0.05593251061 | 3.437365791 | 0.8593414479 | 121.6724251 | 486.6897006 | 31.19805773
4 | 3.410737959 | 0.05879860816 | 3.411244744 | 0.852811186 | 120.5399 | 482.1596001 | 30.134975
4.1 | 3.383850289 | 0.06173630224 | 3.384413413 | 0.8461033532 | 119.3798945 | 477.5195781 | 29.11704744
4.2 | 3.356247686 | 0.06474559286 | 3.356872133 | 0.8392180333 | 118.1926899 | 472.7707597 | 28.14111665
4.3 | 3.32793015 | 0.06782648 | 3.328621263 | 0.8321553158 | 116.9785753 | 467.9143011 | 27.20431983
4.4 | 3.298897682 | 0.07097896367 | 3.299661184 | 0.8249152959 | 115.7378476 | 462.9513903 | 26.30405627
4.5 | 3.269150281 | 0.07420304388 | 3.269992301 | 0.8174980753 | 114.4708117 | 457.8832469 | 25.43795816
4.6 | 3.238687947 | 0.07749872061 | 3.23961505 | 0.8099037624 | 113.1777805 | 452.7111221 | 24.60386533
4.7 | 3.207510681 | 0.08086599388 | 3.208529893 | 0.8021324733 | 111.859075 | 447.4362998 | 23.79980318
4.8 | 3.175618482 | 0.08430486367 | 3.176737328 | 0.794184332 | 110.515024 | 442.0600961 | 23.02396334
4.9 | 3.14301135 | 0.08781533 | 3.144237885 | 0.7860594713 | 109.1459649 | 436.5838596 | 22.27468671
5 | 3.109689286 | 0.09139739286 | 3.111032134 | 0.7777580334 | 107.7522431 | 431.0089724 | 21.55044862
5.1 | 3.075652289 | 0.09505105224 | 3.077120684 | 0.769280171 | 106.3342124 | 425.3368498 | 20.84984558
5.2 | 3.040900359 | 0.09877630816 | 3.042504191 | 0.7606260478 | 104.8922352 | 419.5689408 | 20.17158369
5.3 | 3.005433497 | 0.1025731606 | 3.00718336 | 0.7517958399 | 103.4266823 | 413.706729 | 19.51446835
5.4 | 2.969251702 | 0.1064416096 | 2.971158947 | 0.7427897367 | 101.9379331 | 407.7517325 | 18.87739503
5.5 | 2.932354974 | 0.1103816551 | 2.934431769 | 0.7336079422 | 100.4263762 | 401.7055049 | 18.25934113
5.6 | 2.894743314 | 0.1143932971 | 2.897002707 | 0.7242506766 | 98.89240891 | 395.5696356 | 17.65935873
5.7 | 2.856416721 | 0.1184765357 | 2.858872711 | 0.7147181777 | 97.33643768 | 389.3457507 | 17.07656801
5.8 | 2.817375196 | 0.1226313708 | 2.82004281 | 0.7050107024 | 95.75887843 | 383.0355137 | 16.51015145
5.9 | 2.777618738 | 0.1268578024 | 2.780514117 | 0.6951285292 | 94.16015658 | 376.6406263 | 15.95934857
6 | 2.737147347 | 0.1311558306 | 2.740287841 | 0.6850719602 | 92.54070738 | 370.1628295 | 15.42345123
6.1 | 2.695961023 | 0.1355254553 | 2.699365294 | 0.6748413234 | 90.90097616 | 363.6039046 | 14.90179937
6.2 | 2.654059767 | 0.1399666765 | 2.657747904 | 0.6644369759 | 89.24141864 | 356.9656746 | 14.3937772
6.3 | 2.611443579 | 0.1444794943 | 2.615437227 | 0.6538593067 | 87.56250129 | 350.2500052 | 13.89880973
6.4 | 2.568112457 | 0.1490639086 | 2.572434963 | 0.6431087409 | 85.86470172 | 343.4588069 | 13.41635964
6.5 | 2.524066403 | 0.1537199194 | 2.528742972 | 0.6321857431 | 84.14850916 | 336.5940366 | 12.94592449
6.6 | 2.479305416 | 0.1584475267 | 2.484363292 | 0.621090823 | 82.41442492 | 329.6576997 | 12.48703408
6.7 | 2.433829497 | 0.1632467306 | 2.43929816 | 0.6098245401 | 80.66296306 | 322.6518522 | 12.03924822
6.8 | 2.387638645 | 0.168117531 | 2.393550042 | 0.5983875105 | 78.89465103 | 315.5786041 | 11.60215456
6.9 | 2.34073286 | 0.173059928 | 2.347121655 | 0.5867804137 | 77.11003047 | 308.4401219 | 11.17536673
7 | 2.293112143 | 0.1780739214 | 2.300016005 | 0.5750040011 | 75.30965812 | 301.2386325 | 10.75852259
7.1 | 2.244776493 | 0.1831595114 | 2.252236424 | 0.563059106 | 73.49410688 | 293.9764275 | 10.35128266
7.2 | 2.19572591 | 0.188316698 | 2.203786617 | 0.5509466541 | 71.66396706 | 286.6558682 | 9.953328758
7.3 | 2.145960395 | 0.193545481 | 2.15467071 | 0.5386676776 | 69.81984779 | 279.2793912 | 9.564362711
7.4 | 2.095479947 | 0.1988458606 | 2.104893319 | 0.5262233297 | 67.96237875 | 271.849515 | 9.184105237
7.5 | 2.044284566 | 0.2042178367 | 2.054459616 | 0.513614904 | 66.09221215 | 264.3688486 | 8.812294953
7.6 | 1.992374253 | 0.2096614094 | 2.003375419 | 0.5008438548 | 64.21002509 | 256.8401004 | 8.448687512
7.7 | 1.939749007 | 0.2151765786 | 1.951647297 | 0.4879118242 | 62.31652241 | 249.2660897 | 8.093054859
7.8 | 1.886408829 | 0.2207633443 | 1.899282686 | 0.4748206716 | 60.41244002 | 241.6497601 | 7.745184618
7.9 | 1.832353717 | 0.2264217065 | 1.846290046 | 0.4615725115 | 58.49854896 | 233.9941958 | 7.404879615
8 | 1.777583673 | 0.2321516653 | 1.792679032 | 0.448169758 | 56.57566029 | 226.3026412 | 7.071957536
8.1 | 1.722098697 | 0.2379532206 | 1.738460715 | 0.4346151787 | 54.64463107 | 218.5785243 | 6.746250749
8.2 | 1.665898788 | 0.2438263724 | 1.683647846 | 0.4209119616 | 52.70637156 | 210.8254862 | 6.427606288
8.3 | 1.608983946 | 0.2497711208 | 1.628255186 | 0.4070637965 | 50.76185423 | 203.0474169 | 6.115886052
8.4 | 1.551354171 | 0.2557874657 | 1.572299905 | 0.3930749764 | 48.81212483 | 195.2484993 | 5.810967241
8.5 | 1.493009464 | 0.2618754071 | 1.515802094 | 0.3789505236 | 46.85831619 | 187.4332648 | 5.512743081
8.6 | 1.433949824 | 0.2680349451 | 1.458785396 | 0.3646963489 | 44.90166568 | 179.6066627 | 5.221123916
8.7 | 1.374175252 | 0.2742660796 | 1.401277812 | 0.3503194529 | 42.9435372 | 171.7741488 | 4.936038758
8.8 | 1.313685747 | 0.2805688106 | 1.343312733 | 0.3358281833 | 40.98544942 | 163.9417977 | 4.657437434
8.9 | 1.252481309 | 0.2869431382 | 1.284930268 | 0.3212325671 | 39.02911213 | 156.1164485 | 4.385293498
9 | 1.190561939 | 0.2933890622 | 1.226178972 | 0.3065447431 | 37.07647361 | 148.3058944 | 4.119608179
9.1 | 1.127927636 | 0.2999065829 | 1.167118122 | 0.2917795304 | 35.12978284 | 140.5191314 | 3.860415697
9.2 | 1.0645784 | 0.3064957 | 1.107820736 | 0.2769551841 | 33.19167231 | 132.7666893 | 3.607790469
9.3 | 1.000514232 | 0.3131564137 | 1.048377636 | 0.2620944089 | 31.265269 | 125.061076 | 3.361856882
9.4 | 0.9357351306 | 0.3198887239 | 0.9889029428 | 0.2472257357 | 29.35434508 | 117.4173803 | 3.122802668
9.5 | 0.8702410969 | 0.3266926306 | 0.9295416299 | 0.2323854075 | 27.46352449 | 109.854098 | 2.890897315
9.6 | 0.8040321306 | 0.3335681339 | 0.8704799636 | 0.2176199909 | 25.59856889 | 102.3942755 | 2.666517592
9.7 | 0.7371082316 | 0.3405152337 | 0.8119600788 | 0.2029900197 | 23.76677661 | 95.06710645 | 2.450183156
9.8 | 0.6694694 | 0.34753393 | 0.754300411 | 0.1885751028 | 21.97754207 | 87.91016827 | 2.242606333
9.9 | 0.6011156357 | 0.3546242229 | 0.6979243132 | 0.1744810783 | 20.24313911 | 80.97255645 | 2.044761527
10 | 0.5320469388 | 0.3617861122 | 0.6433996706 | 0.1608499176 | 18.5798056 | 74.31922239 | 1.85798056
10.1 | 0.4622633092 | 0.3690195982 | 0.5914920379 | 0.1478730095 | 17.00919804 | 68.03679216 | 1.684079014
10.2 | 0.3917647469 | 0.3763246806 | 0.5432309658 | 0.1358077414 | 15.56020741 | 62.24082964 | 1.52551053
10.3 | 0.320551252 | 0.3837013596 | 0.4999798381 | 0.1249949595 | 14.27087099 | 57.08348396 | 1.385521455
10.4 | 0.2486228245 | 0.3911496351 | 0.4634774492 | 0.1158693623 | 13.18951063 | 52.75804252 | 1.268222176
10.5 | 0.1759794643 | 0.3986695071 | 0.4357822252 | 0.1089455563 | 12.37320571 | 49.49282285 | 1.178400544
10.6 | 0.1026211714 | 0.4062609757 | 0.4190215808 | 0.1047553952 | 11.88093151 | 47.52372604 | 1.120842595
10.7 | 0.02854794592 | 0.4139240408 | 0.4149073352 | 0.1037268338 | 11.76029306 | 47.04117224 | 1.099092809
10.8 | 0 | 0.4216587024 | 0.4216587024 | 0.1054146756 | 11.95829908 | 47.83319631 | 1.107249915
10.9 | 0 | 0.4294649606 | 0.4294649606 | 0.1073662402 | 12.1875084 | 48.75003361 | 1.118120037
11 | 0 | 0.4373428153 | 0.4373428153 | 0.1093357038 | 12.41910827 | 49.67643309 | 1.129009843
11.1 | 0 | 0.4452922665 | 0.4452922665 | 0.1113230666 | 12.65310658 | 50.61242633 | 1.139919512
11.2 | 0 | 0.4533133143 | 0.4533133143 | 0.1133283286 | 12.8895113 | 51.55804521 | 1.150849223
11.3 | 0 | 0.4614059586 | 0.4614059586 | 0.1153514896 | 13.12833047 | 52.51332188 | 1.161799157
11.4 | 0 | 0.4695701994 | 0.4695701994 | 0.1173925498 | 13.3695722 | 53.4782888 | 1.172769491
11.5 | 0 | 0.4778060367 | 0.4778060367 | 0.1194515092 | 13.61324468 | 54.4529787 | 1.183760407
11.6 | 0 | 0.4861134706 | 0.4861134706 | 0.1215283677 | 13.85935615 | 55.4374246 | 1.194772082
11.7 | 0 | 0.494492501 | 0.494492501 | 0.1236231253 | 14.10791495 | 56.43165981 | 1.205804697
11.8 | 0 | 0.502943128 | 0.502943128 | 0.125735782 | 14.35892948 | 57.43571792 | 1.21685843
11.9 | 0 | 0.5114653514 | 0.5114653514 | 0.1278663379 | 14.61240821 | 58.44963282 | 1.227933463
12 | 0 | 0.5200591714 | 0.5200591714 | 0.1300147929 | 14.86835967 | 59.47343868 | 1.239029973
12.1 | 0 | 0.528724588 | 0.528724588 | 0.132181147 | 15.12679249 | 60.50716996 | 1.25014814
12.2 | 0 | 0.537461601 | 0.537461601 | 0.1343654003 | 15.38771535 | 61.55086139 | 1.261288143
12.3 | 0 | 0.5462702106 | 0.5462702106 | 0.1365675527 | 15.65113701 | 62.60454802 | 1.272450163
12.4 | 0 | 0.5551504167 | 0.5551504167 | 0.1387876042 | 15.91706629 | 63.66826516 | 1.283634378
12.5 | 0 | 0.5641022194 | 0.5641022194 | 0.1410255548 | 16.1855121 | 64.74204841 | 1.294840968
12.6 | 0 | 0.5731256186 | 0.5731256186 | 0.1432814046 | 16.45648342 | 65.82593367 | 1.306070113
12.7 | 0 | 0.5822206143 | 0.5822206143 | 0.1455551536 | 16.72998928 | 66.91995712 | 1.317321991
12.8 | 0 | 0.5913872065 | 0.5913872065 | 0.1478468016 | 17.0060388 | 68.02415522 | 1.328596782
12.9 | 0 | 0.6006253953 | 0.6006253953 | 0.1501563488 | 17.28464118 | 69.13856473 | 1.339894665
13 | 0 | 0.6099351806 | 0.6099351806 | 0.1524837952 | 17.56580567 | 70.26322268 | 1.351215821
13.1 | 0 | 0.6193165624 | 0.6193165624 | 0.1548291406 | 17.8495416 | 71.39816641 | 1.362560428
13.2 | 0 | 0.6287695408 | 0.6287695408 | 0.1571923852 | 18.13585838 | 72.54343353 | 1.373928665
13.3 | 0 | 0.6382941157 | 0.6382941157 | 0.1595735289 | 18.42476549 | 73.69906195 | 1.385320713
13.4 | 0 | 0.6478902871 | 0.6478902871 | 0.1619725718 | 18.71627246 | 74.86508985 | 1.396736751
13.5 | 0 | 0.6575580551 | 0.6575580551 | 0.1643895138 | 19.01038893 | 76.0415557 | 1.408176957
13.6 | 0 | 0.6672974196 | 0.6672974196 | 0.1668243549 | 19.30712457 | 77.22849828 | 1.419641512
13.7 | 0 | 0.6771083806 | 0.6771083806 | 0.1692770952 | 19.60648916 | 78.42595662 | 1.431130595
13.8 | 0 | 0.6869909382 | 0.6869909382 | 0.1717477345 | 19.90849252 | 79.63397008 | 1.442644385
13.9 | 0 | 0.6969450922 | 0.6969450922 | 0.1742362731 | 20.21314457 | 80.85257826 | 1.454183062
14 | 0 | 0.7069708429 | 0.7069708429 | 0.1767427107 | 20.52045527 | 82.0818211 | 1.465746805
14.1 | 0 | 0.71706819 | 0.71706819 | 0.1792670475 | 20.83043469 | 83.32173877 | 1.477335794
14.2 | 0 | 0.7272371337 | 0.7272371337 | 0.1818092834 | 21.14309294 | 84.57237177 | 1.488950207
14.3 | 0 | 0.7374776739 | 0.7374776739 | 0.1843694185 | 21.45844022 | 85.83376088 | 1.500590225
14.4 | 0 | 0.7477898106 | 0.7477898106 | 0.1869474527 | 21.77648679 | 87.10594714 | 1.512256027
14.5 | 0 | 0.7581735439 | 0.7581735439 | 0.189543386 | 22.09724298 | 88.38897191 | 1.523947792
14.6 | 0 | 0.7686288737 | 0.7686288737 | 0.1921572184 | 22.42071921 | 89.68287683 | 1.535665699
14.7 | 0 | 0.7791558 | 0.7791558 | 0.19478895 | 22.74692595 | 90.9877038 | 1.547409929
14.8 | 0 | 0.7897543229 | 0.7897543229 | 0.1974385807 | 23.07587376 | 92.30349505 | 1.55918066
14.9 | 0 | 0.8004244422 | 0.8004244422 | 0.2001061106 | 23.40757326 | 93.63029306 | 1.570978071
15 | 0 | 0.8111661582 | 0.8111661582 | 0.2027915395 | 23.74203515 | 94.96814061 | 1.582802344
15.1 | 0 | 0.8219794706 | 0.8219794706 | 0.2054948677 | 24.0792702 | 96.31708079 | 1.594653655
15.2 | 0 | 0.8328643796 | 0.8328643796 | 0.2082160949 | 24.41928923 | 97.67715693 | 1.606532186
15.3 | 0 | 0.8438208851 | 0.8438208851 | 0.2109552213 | 24.76210317 | 99.0484127 | 1.618438116
15.4 | 0 | 0.8548489871 | 0.8548489871 | 0.2137122468 | 25.107723 | 100.430892 | 1.630371623
15.5 | 0 | 0.8659486857 | 0.8659486857 | 0.2164871714 | 25.45615977 | 101.8246391 | 1.642332888
15.6 | 0 | 0.8771199808 | 0.8771199808 | 0.2192799952 | 25.8074246 | 103.2296984 | 1.65432209
15.7 | 0 | 0.8883628724 | 0.8883628724 | 0.2220907181 | 26.1615287 | 104.6461148 | 1.666339408
15.8 | 0 | 0.8996773606 | 0.8996773606 | 0.2249193402 | 26.51848334 | 106.0739334 | 1.678385021
15.9 | 0 | 0.9110634453 | 0.9110634453 | 0.2277658613 | 26.87829985 | 107.5131994 | 1.69045911
16 | 0 | 0.9225211265 | 0.9225211265 | 0.2306302816 | 27.24098965 | 108.9639586 | 1.702561853
16.1 | 0 | 0.9340504043 | 0.9340504043 | 0.2335126011 | 27.60656422 | 110.4262569 | 1.71469343
16.2 | 0 | 0.9456512786 | 0.9456512786 | 0.2364128196 | 27.97503513 | 111.9001405 | 1.72685402
16.3 | 0 | 0.9573237494 | 0.9573237494 | 0.2393309373 | 28.34641399 | 113.385656 | 1.739043803
16.4 | 0 | 0.9690678167 | 0.9690678167 | 0.2422669542 | 28.72071252 | 114.8828501 | 1.751262958
16.5 | 0 | 0.9808834806 | 0.9808834806 | 0.2452208702 | 29.09794247 | 116.3917699 | 1.763511665
16.6 | 0 | 0.992770741 | 0.992770741 | 0.2481926853 | 29.47811571 | 117.9124628 | 1.775790103
16.7 | 0 | 1.004729598 | 1.004729598 | 0.2511823995 | 29.86124413 | 119.4449765 | 1.788098451
16.8 | 0 | 1.016760051 | 1.016760051 | 0.2541900129 | 30.24733973 | 120.9893589 | 1.800436889
16.9 | 0 | 1.028862101 | 1.028862101 | 0.2572155254 | 30.63641457 | 122.5456583 | 1.812805596
17 | 0 | 1.041035748 | 1.041035748 | 0.260258937 | 31.02848078 | 124.1139231 | 1.825204752
17.1 | 0 | 1.053280991 | 1.053280991 | 0.2633202478 | 31.42355055 | 125.6942022 | 1.837634535
17.2 | 0 | 1.065597831 | 1.065597831 | 0.2663994577 | 31.82163618 | 127.2865447 | 1.850095127
17.3 | 0 | 1.077986267 | 1.077986267 | 0.2694965667 | 32.22274999 | 128.891 | 1.862586705
17.4 | 0 | 1.090446299 | 1.090446299 | 0.2726115748 | 32.62690442 | 130.5076177 | 1.875109449
17.5 | 0 | 1.102977929 | 1.102977929 | 0.2757444821 | 33.03411194 | 132.1364478 | 1.88766354
17.6 | 0 | 1.115581154 | 1.115581154 | 0.2788952886 | 33.44438513 | 133.7775405 | 1.900249155
17.7 | 0 | 1.128255977 | 1.128255977 | 0.2820639941 | 33.8577366 | 135.4309464 | 1.912866475
17.8 | 0 | 1.141002395 | 1.141002395 | 0.2852505988 | 34.27417908 | 137.0967163 | 1.925515679
17.9 | 0 | 1.153820411 | 1.153820411 | 0.2884551027 | 34.69372534 | 138.7749013 | 1.938196946
18 | 0 | 1.166710022 | 1.166710022 | 0.2916775056 | 35.11638821 | 140.4655529 | 1.950910456
18.1 | 0 | 1.179671231 | 1.179671231 | 0.2949178077 | 35.54218064 | 142.1687225 | 1.963656389
18.2 | 0 | 1.192704036 | 1.192704036 | 0.2981760089 | 35.97111559 | 143.8844624 | 1.976434923
18.3 | 0 | 1.205808437 | 1.205808437 | 0.3014521093 | 36.40320615 | 145.6128246 | 1.989246238
18.4 | 0 | 1.218984435 | 1.218984435 | 0.3047461088 | 36.83846545 | 147.3538618 | 2.002090513
18.5 | 0 | 1.23223203 | 1.23223203 | 0.3080580074 | 37.27690669 | 149.1076267 | 2.014967929
18.6 | 0 | 1.245551221 | 1.245551221 | 0.3113878052 | 37.71854315 | 150.8741726 | 2.027878664
18.7 | 0 | 1.258942008 | 1.258942008 | 0.314735502 | 38.16338818 | 152.6535527 | 2.040822897
18.8 | 0 | 1.272404392 | 1.272404392 | 0.3181010981 | 38.61145521 | 154.4458209 | 2.053800809
18.9 | 0 | 1.285938373 | 1.285938373 | 0.3214845932 | 39.06275774 | 156.2510309 | 2.066812579
19 | 0 | 1.29954395 | 1.29954395 | 0.3248859875 | 39.51730931 | 158.0692373 | 2.079858385
19.1 | 0 | 1.313221124 | 1.313221124 | 0.3283052809 | 39.97512359 | 159.9004943 | 2.092938408
19.2 | 0 | 1.326969894 | 1.326969894 | 0.3317424735 | 40.43621426 | 161.7448571 | 2.106052826
19.3 | 0 | 1.340790261 | 1.340790261 | 0.3351975652 | 40.90059513 | 163.6023805 | 2.11920182
19.4 | 0 | 1.354682224 | 1.354682224 | 0.338670556 | 41.36828003 | 165.4731201 | 2.132385569
19.5 | 0 | 1.368645784 | 1.368645784 | 0.3421614459 | 41.8392829 | 167.3571316 | 2.145604251
19.6 | 0 | 1.38268094 | 1.38268094 | 0.345670235 | 42.31361773 | 169.2544709 | 2.158858047
19.7 | 0 | 1.396787693 | 1.396787693 | 0.3491969232 | 42.79129858 | 171.1651943 | 2.172147136
19.8 | 0 | 1.410966042 | 1.410966042 | 0.3527415106 | 43.27233961 | 173.0893585 | 2.185471698
19.9 | 0 | 1.425215988 | 1.425215988 | 0.356303997 | 43.75675502 | 175.0270201 | 2.198831911
20 | 0 | 1.439537531 | 1.439537531 | 0.3598843827 | 44.2445591 | 176.9782364 | 2.212227955
20.1 | 0 | 1.45393067 | 1.45393067 | 0.3634826674 | 44.7357662 | 178.9430648 | 2.22566001
20.2 | 0 | 1.468395405 | 1.468395405 | 0.3670988513 | 45.23039074 | 180.921563 | 2.239128255
20.3 | 0 | 1.482931737 | 1.482931737 | 0.3707329343 | 45.72844724 | 182.913789 | 2.252632869
20.4 | 0 | 1.497539666 | 1.497539666 | 0.3743849164 | 46.22995026 | 184.919801 | 2.266174032
20.5 | 0 | 1.512219191 | 1.512219191 | 0.3780547977 | 46.73491443 | 186.9396577 | 2.279751924
20.6 | 0 | 1.526970312 | 1.526970312 | 0.3817425781 | 47.24335449 | 188.9734179 | 2.293366723
20.7 | 0 | 1.541793031 | 1.541793031 | 0.3854482577 | 47.7552852 | 191.0211408 | 2.307018609
20.8 | 0 | 1.556687345 | 1.556687345 | 0.3891718363 | 48.27072144 | 193.0828857 | 2.320707761
20.9 | 0 | 1.571653257 | 1.571653257 | 0.3929133141 | 48.78967812 | 195.1587125 | 2.33443436
21 | 0 | 1.586690764 | 1.586690764 | 0.3966726911 | 49.31217026 | 197.2486811 | 2.348198584
21.1 | 0 | 1.601799869 | 1.601799869 | 0.4004499671 | 49.83821293 | 199.3528517 | 2.362000613
21.2 | 0 | 1.616980569 | 1.616980569 | 0.4042451423 | 50.36782126 | 201.471285 | 2.375840626
21.3 | 0 | 1.632232867 | 1.632232867 | 0.4080582167 | 50.90101048 | 203.6040419 | 2.389718802
21.4 | 0 | 1.647556761 | 1.647556761 | 0.4118891902 | 51.43779588 | 205.7511835 | 2.403635322
21.5 | 0 | 1.662952251 | 1.662952251 | 0.4157380628 | 51.97819282 | 207.9127713 | 2.417590364
21.6 | 0 | 1.678419338 | 1.678419338 | 0.4196048345 | 52.52221672 | 210.0888669 | 2.431584107
21.7 | 0 | 1.693958021 | 1.693958021 | 0.4234895054 | 53.06988309 | 212.2795324 | 2.445616732
21.8 | 0 | 1.709568301 | 1.709568301 | 0.4273920754 | 53.62120752 | 214.4848301 | 2.459688418
21.9 | 0 | 1.725250178 | 1.725250178 | 0.4313125445 | 54.17620563 | 216.7048225 | 2.473799344
22 | 0 | 1.741003651 | 1.741003651 | 0.4352509128 | 54.73489317 | 218.9395727 | 2.487949689
22.1 | 0 | 1.756828721 | 1.756828721 | 0.4392071802 | 55.29728591 | 221.1891436 | 2.502139634
22.2 | 0 | 1.772725387 | 1.772725387 | 0.4431813467 | 55.86339971 | 223.4535989 | 2.516369356
22.3 | 0 | 1.788693649 | 1.788693649 | 0.4471734123 | 56.43325052 | 225.7330021 | 2.530639037
22.4 | 0 | 1.804733509 | 1.804733509 | 0.4511833771 | 57.00685434 | 228.0274174 | 2.544948855
22.5 | 0 | 1.820844964 | 1.820844964 | 0.4552112411 | 57.58422725 | 230.336909 | 2.559298989
22.6 | 0 | 1.837028017 | 1.837028017 | 0.4592570041 | 58.16538539 | 232.6615416 | 2.573689619
22.7 | 0 | 1.853282665 | 1.853282665 | 0.4633206663 | 58.75034499 | 235.00138 | 2.588120925
22.8 | 0 | 1.869608911 | 1.869608911 | 0.4674022277 | 59.33912235 | 237.3564894 | 2.602593085
22.9 | 0 | 1.886006752 | 1.886006752 | 0.4715016881 | 59.93173382 | 239.7269353 | 2.61710628
23 | 0 | 1.902476191 | 1.902476191 | 0.4756190477 | 60.52819584 | 242.1127834 | 2.631660689
23.1 | 0 | 1.919017226 | 1.919017226 | 0.4797543064 | 61.12852493 | 244.5140997 | 2.646256491
23.2 | 0 | 1.935629857 | 1.935629857 | 0.4839074643 | 61.73273766 | 246.9309507 | 2.660893865
23.3 | 0 | 1.952314085 | 1.952314085 | 0.4880785213 | 62.34085069 | 249.3634028 | 2.675572991
23.4 | 0 | 1.96906991 | 1.96906991 | 0.4922674774 | 62.95288074 | 251.8115229 | 2.690294049
23.5 | 0 | 1.985897331 | 1.985897331 | 0.4964743327 | 63.5688446 | 254.2753784 | 2.705057217
23.6 | 0 | 2.002796348 | 2.002796348 | 0.500699087 | 64.18875914 | 256.7550366 | 2.719862675
23.7 | 0 | 2.019766962 | 2.019766962 | 0.5049417406 | 64.8126413 | 259.2505652 | 2.734710604
23.8 | 0 | 2.036809173 | 2.036809173 | 0.5092022932 | 65.4405081 | 261.7620324 | 2.749601181
23.9 | 0 | 2.05392298 | 2.05392298 | 0.513480745 | 66.07237661 | 264.2895065 | 2.764534586
24 | 0 | 2.071108384 | 2.071108384 | 0.5177770959 | 66.708264 | 266.833056 | 2.779511
24.1 | 0 | 2.088365384 | 2.088365384 | 0.522091346 | 67.34818748 | 269.3927499 | 2.794530601
24.2 | 0 | 2.105693981 | 2.105693981 | 0.5264234952 | 67.99216435 | 271.9686574 | 2.809593568
24.3 | 0 | 2.123094174 | 2.123094174 | 0.5307735435 | 68.64021199 | 274.560848 | 2.824700082
24.4 | 0 | 2.140565964 | 2.140565964 | 0.5351414909 | 69.29234783 | 277.1693913 | 2.839850321
24.5 | 0 | 2.15810935 | 2.15810935 | 0.5395273375 | 69.9485894 | 279.7943576 | 2.855044465
24.6 | 0 | 2.175724333 | 2.175724333 | 0.5439310832 | 70.60895426 | 282.4358171 | 2.870282694
24.7 | 0 | 2.193410912 | 2.193410912 | 0.5483527281 | 71.27346009 | 285.0938404 | 2.885565186
24.8 | 0 | 2.211169088 | 2.211169088 | 0.552792272 | 71.94212461 | 287.7684985 | 2.900892122
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

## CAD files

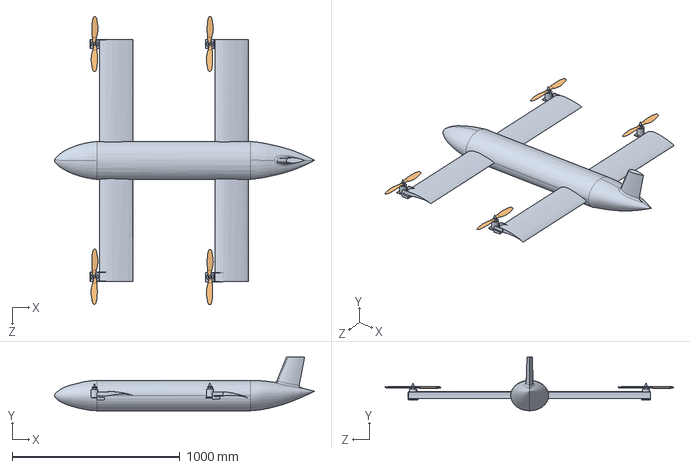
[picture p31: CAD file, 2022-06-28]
Aerodynamics Design/VTOL wing end.SLDASM
1549.2 x 319.5 x 1718.9 mm
VTOL Wing end
Propeller_1340 x 4

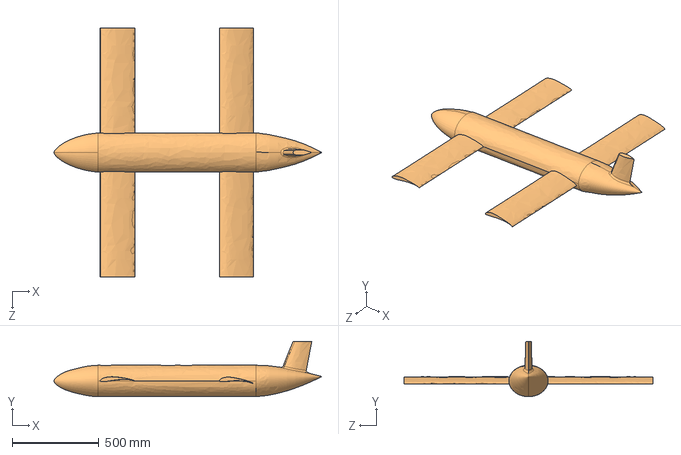
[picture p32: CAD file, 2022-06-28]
Aerodynamics Design/Solidworks Model.STEP
1549.2 x 319.5 x 1441.7 mm

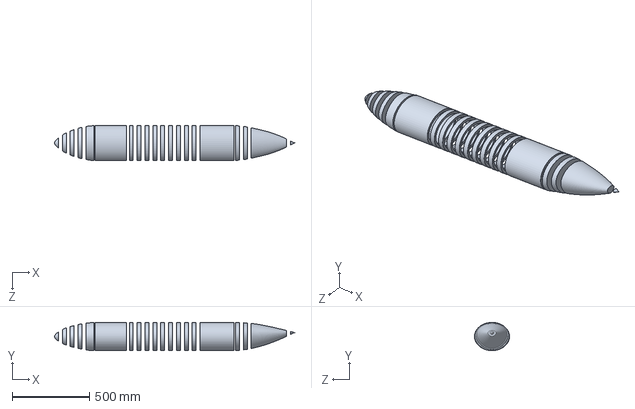
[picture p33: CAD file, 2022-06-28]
Aerodynamics Design/TRY 1 (NOSE + TAIL) sections.SLDPRT
1549.2 x 181.8 x 226.2 mm

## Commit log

2022-06-19 Initialize Team Tracker
    [The Hive Tracker.xlsx]
2022-06-19 Add Control & Computing Systems Tracker
    [Control & Computing System Tracker.xlsx]
2022-06-20 Add spraying nozzle suggestion
2022-06-20 Add another nozzle suggestion
2022-06-20 Add water pump suggestion
2022-06-20 Add another water pump suggestion
2022-06-20 Add battery suggestion
2022-06-20 Create Nose + Fuselage CAD Model
    [Solidworks Model.SLDPRT]
2022-06-20 Add tail to CAD model
    [Solidworks Model.SLDPRT]
2022-06-20 Update the CAD model
    [Solidworks Model.SLDPRT]
2022-06-20 Design V1
    [Base and Rotor System.SLDASM, Base.SLDPRT, Solidworks Model.SLDPRT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]
2022-06-20 Design V2
    [Base and Rotor System.SLDASM, Base.SLDPRT, Tilt Rotor.SLDPRT]
2022-06-20 Create Step file
    [Base and Rotor System.SLDASM, Base.SLDPRT, Solidworks Model.STEP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]
2022-06-20 Modify Design
    [Solidworks Model.SLDPRT, Solidworks Model.STEP]
2022-06-20 Modify CAD model
    [Solidworks Model.SLDPRT, Solidworks Model.STEP]
2022-06-21 Add ESC for Pump 03
2022-06-21 Add 30A ESC suggestion
2022-06-21 Add another ESC suggestion
2022-06-21 Add transition Servo suggestion
2022-06-21 Add another transition Servo
2022-06-21 Initialize Mission Requirement Calculator
    [Power Consumption.xlsx]
2022-06-21 Create excel sheet for spraying specs
    [Spraying Mechanism Specifications.xlsx]
2022-06-21 Create excel sheet for Control System specs
    [Components Specifications.xlsx]
2022-06-22 Add drag & lift values to excel sheet
    [Power Consumption.xlsx]
2022-06-22 Add thrust & power data
    [Power Consumption.xlsx]
2022-06-22 Add thrust function of MN5008 KV170 P17*5.8'' CF
2022-06-22 Add thrust function of MN5008 KV170 P18*6.1''CF
2022-06-22 Add thrust function of MN5008 KV340 P17*5.8''CF
2022-06-22 Add thrust function of MN5008 KV340 P18*6.1''CF
2022-06-22 Add thrust function of MN5008 KV400 P15*5''CF
2022-06-22 Add thrust function of MN5008 KV400 P16*5.4''CF
2022-06-22 Add thrust function of MN5008 KV400 P17*5.8''CF
2022-06-22 Modify Power Consumption excel sheet
    [Power Consumption.xlsx]
2022-06-22 Calculate Cruise Speed with Payload
    [Power Consumption.xlsx]
2022-06-22 Calculate cruise speed without payload
    [Power Consumption.xlsx]
2022-06-22 Calculate mission power & energy consumed in cruise
    [Power Consumption.xlsx]
2022-06-22 Graph power to thrust MN5008 KV170 P17*5.8''CF
2022-06-22 Graph power to thrust MN5008 KV170 P18*6.1''CF
2022-06-22 Graph power to thrust MN5008 KV340 P17*5.8''CF
2022-06-22 Graph power to thrust MN5008 KV340 P18*6.1''CF
2022-06-22 Graph power to thrust MN5008 KV400 P15*5''CF
2022-06-22 Graph power to thrust MN5008 KV400 P16*5.4''CF
2022-06-22 Graph power to thrust MN5008 KV400 P17*5.8''CF
2022-06-22 Graph Power against Thrust for all motors in Desmos
2022-06-22 Graph Thrust against Power for all motors in Desmos
2022-06-22 Calculate Power & Energy Consumption for Take-off + Landing
    [Power Consumption.xlsx]
2022-06-22 Calculate Time & Distance for flight transition
    [Power Consumption.xlsx]
2022-06-22 Add files via upload
    Model for VTOL Simulation with prop at wing end.
    [VTOL wing end.SLDASM]
2022-06-22 Add calculations for spray zone
    [Power Consumption.xlsx]
2022-06-22 Modify Power consumption calculations
    [Power Consumption.xlsx]
2022-06-22 Update Team Tracker
    [The Hive Tracker.xlsx]
2022-06-23 Write Propulsion CDR
    [Power Consumption.xlsx]
2022-06-24 Add fritzing schematic for Electrical Components
    [Electrical Components.fzz]
2022-06-25 Modified Power Consumption Calculations
    [Power Consumption.xlsx]
2022-06-27 Modified The Hive Tracker
    [The Hive Tracker.xlsx]
2022-06-28 Added Path Optimization for fixed wing
2022-06-28 Added Battery to safety table
2022-06-28 Moved CAD models to Aerodynamics folder
    [TRY 1 (NOSE + TAIL) sections.SLDPRT, VTOL wing end.SLDASM]
2022-06-30 Added Cost list excel sheet
    [Cost list.xlsx]
2022-07-04 Deleted Cost List Excel Sheet
    [Cost list.xlsx]
